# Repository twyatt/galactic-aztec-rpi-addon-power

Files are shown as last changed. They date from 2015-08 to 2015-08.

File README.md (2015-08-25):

# About

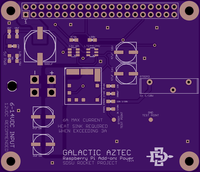
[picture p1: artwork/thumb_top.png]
OSHPark PCB Top Thumbnail

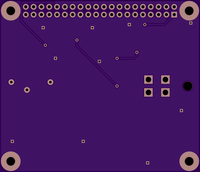
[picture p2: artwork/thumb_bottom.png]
OSHPark PCB Bottom Thumbnail


Board designed to provide external power (e.g. using 2-3S LiPo batteries) for Raspberry Pis onboard the [Galactic Aztec] rocket.

Supports 6-14 VDC input and allows tuning of output voltage between 4.64 and 5.27 VDC to the Raspberry Pi 5V GPIO pins.
**NOTE: RTRIM1 is incorrectly labelled as 2k and a 2.5k resistor should be used instead to put the output voltage at the expected range.**

The design features the [LTC4412HV] to act as an [ideal safety diode], which is advised for Raspberry Pi HATs.

*The hope was to utilize the power switch-over features of the [LTC4412HV], allowing for the Raspberry Pi to be powered via USB and upon disconnecting, automatically switch over to the auxiliary power input, but in testing this feature did not function properly. Power was drawn from both sources when connected rather than completely switching between the available power sources.*

Custom EagleCAD parts on this board can be found in the [SDSU Rocket Eagle Libraries].

# Bill of Materials

| Qty | Name | Description | Part Number | Vendor |
|:---:|---|---|---:|---|
| 1 | CI2 | Capacitor 47µF 35V 63mA SMD | [493-2202-1-ND] | DigiKey  |
| 1 | CI1 | Capacitor 22µF 35V 45mA SMD | [493-9805-1-ND] | DigiKey  |
| 1 | R1 | Resistor 100kΩ 1/4W 1% 0603 | [RHM100KADCT-ND]  | DigiKey  |
| 1 | IC1 | DC to DC Converter 6A | [555-1125-1-ND] | DigiKey  |
| 1 | RTRIM1 | Resistor 2kΩ 0603 | [P2.00KHCT-ND] | DigiKey  |
| 1 | RTRIM2 | Resistor 2.49kΩ 0603 | [RHM2.49KCFCT-ND] | DigiKey  |
| 1 | RTRIM3 | Potentiometer 1kΩ 10% 3/4W 20 | [987-1160-ND] | DigiKey  |
| 1 | RTRIM_ALT | Resistor 1.33kΩ 0.1% 1/10W 0603 | [P1.33KDBCT-ND] | DigiKey  |
| 1 | RTUNE | Resistor 220Ω 1% 1/10W 0603 | [RHM220CFCT-ND] | DigiKey  |
| 1 | CTUNE | Capacitor 3900pF 25V 5% | [445-2665-1-ND] | DigiKey  |
| 2 | CO1, CO2  | Capacitor 47µF 35V 63mA SMD | [493-2202-1-ND] | DigiKey  |
| 3 | C[2-4] | Capacitor 10µF 16V 0603 | [490-7198-1-ND] | DigiKey  |
| 1 | R3 | Resistor 470kΩ 1% 1/4W 0603 | [P470KBYCT-ND] | DigiKey  |
| 1 | IC2 | LTC4412HV Source Selector Switch IC SOT-23-6 | [LTC4412HVIS6] | DigiKey  |
| 1 | | MOSFET P-Channel 1.8V Vdss=12V Id=6A SOT23-6 | [FDC606PCT-ND] | DigiKey  |
| 1 | | Capacitor 1000µF 20% 10V 310mA SMD | [493-2171-1-ND] | DigiKey  |
| 1 | | Capacitor 820µF 20% 16V 80mΩ 510mA SMD | [1189-2069-1-ND]  | DigiKey  |
| 1 | | Capacitor 10uF 20% 16V 0603 | [490-7198-1-ND] | DigiKey  |
| 1 | | Molex Mini Fit Jr. 4-pos Right Angle | [WM1352-ND] | DigiKey  |
| 1 | D4 | LED Red Vf=1.8V If=2mA 0603 | [475-1195-2-ND] | DigiKey  |
| 1 | R4 | Resistor 1.8kΩ 1/4W 1% 0603 | [P1.8KBYCT-ND] | DigiKey  |
| 1 | | Header Stacking 2x20 Tall 23mm | [1979] | Adafruit |

[Galactic Aztec]: http://rocket.sdsu.edu/rockets
[LTC4412HV]: http://www.linear.com/product/LTC4412HV
[ideal safety diode]: https://github.com/raspberrypi/hats/blob/master/designguide.md#back-powering-the-pi-via-the-j8-gpio-header
[SDSU Rocket Eagle Libraries]: https://github.com/twyatt/SDSURocket-Eagle-Libraries
[493-2202-1-ND]: http://www.digikey.com/product-detail/en/UWT1V470MCL1GS/493-2202-1-ND/590177
[493-9805-1-ND]: http://www.digikey.com/product-detail/en/UWJ1V220MCL1GB/493-9805-1-ND/3963137
[RHM100KADCT-ND]: http://www.digikey.com/product-detail/en/ESR03EZPF1003/RHM100KADCT-ND/1983754
[555-1125-1-ND]: http://www.digikey.com/product-detail/en/APTS006A0X-SRZ/555-1125-1-ND/1766113
[P2.00KHCT-ND]: http://www.digikey.com/product-detail/en/ERJ-3EKF2001V/P2.00KHCT-ND/198219
[RHM2.49KCFCT-ND]: http://www.digikey.com/product-detail/en/MCR03ERTF2491/RHM2.49KCFCT-ND/2796475
[987-1160-ND]: http://www.digikey.com/product-detail/en/89PR1KLF/987-1160-ND/2408738
[P1.33KDBCT-ND]: http://www.digikey.com/product-detail/en/ERA-3AEB1331V/P1.33KDBCT-ND/3075785
[RHM220CFCT-ND]: http://www.digikey.com/product-detail/en/MCR03ERTF2200/RHM220CFCT-ND/2796470
[445-2665-1-ND]: http://www.digikey.com/product-detail/en/C1608C0G1E392J080AA/445-2665-1-ND/970490
[493-2202-1-ND]: http://www.digikey.com/product-detail/en/UWT1V470MCL1GS/493-2202-1-ND/590177
[490-7198-1-ND]: http://www.digikey.com/product-detail/en/GRM188C81C106MA73D/490-7198-1-ND/3900421
[P470KBYCT-ND]: http://www.digikey.com/product-detail/en/ERJ-PA3F4703V/P470KBYCT-ND/5036197
[LTC4412HVIS6]: http://www.digikey.com/product-detail/en/LTC4412HVIS6%23TRMPBF/LTC4412HVIS6%23TRMPBFCT-ND/3232334
[FDC606PCT-ND]: http://www.digikey.com/product-detail/en/FDC606P/FDC606PCT-ND/1626185
[493-2171-1-ND]: http://www.digikey.com/product-detail/en/UWT1A102MNL1GS/493-2171-1-ND/590146
[1189-2069-1-ND]: http://www.digikey.com/product-detail/en/16TKV820M10X10.5/1189-2069-1-ND/3986988
[490-7198-1-ND]: http://www.digikey.com/product-detail/en/GRM188C81C106MA73D/490-7198-1-ND/3900421
[WM1352-ND]: http://www.digikey.com/product-search/en?x=0&y=0&lang=en&site=us&keywords=538-39-30-1040
[475-1195-2-ND]: http://www.digikey.com/product-detail/en/LS%20L29K-H1J2-1-Z/475-1195-1-ND/810356
[P1.8KBYCT-ND]: http://www.digikey.com/product-detail/en/ERJ-PA3F1801V/P1.8KBYCT-ND/5036145
[1979]: http://www.adafruit.com/products/1979

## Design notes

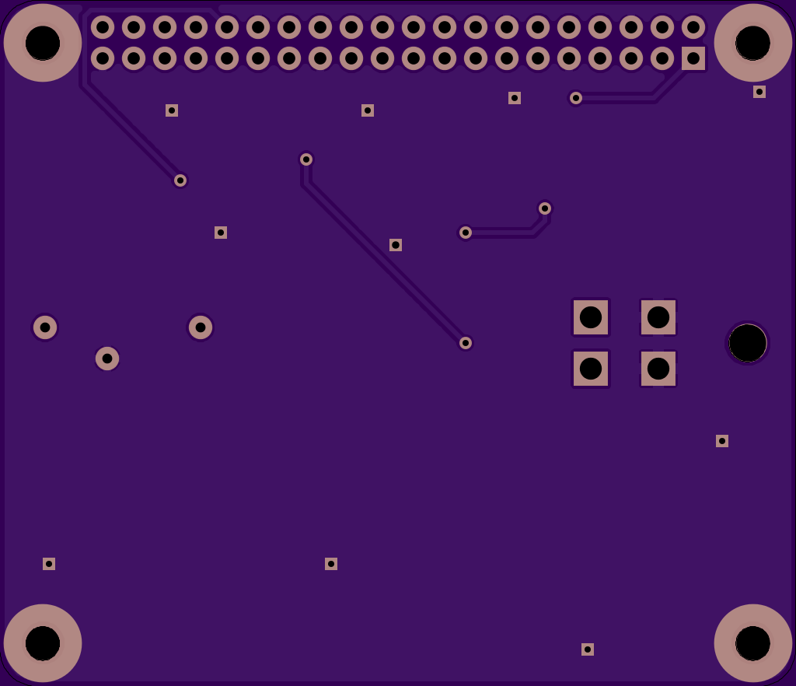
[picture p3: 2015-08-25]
artwork/bottom.png

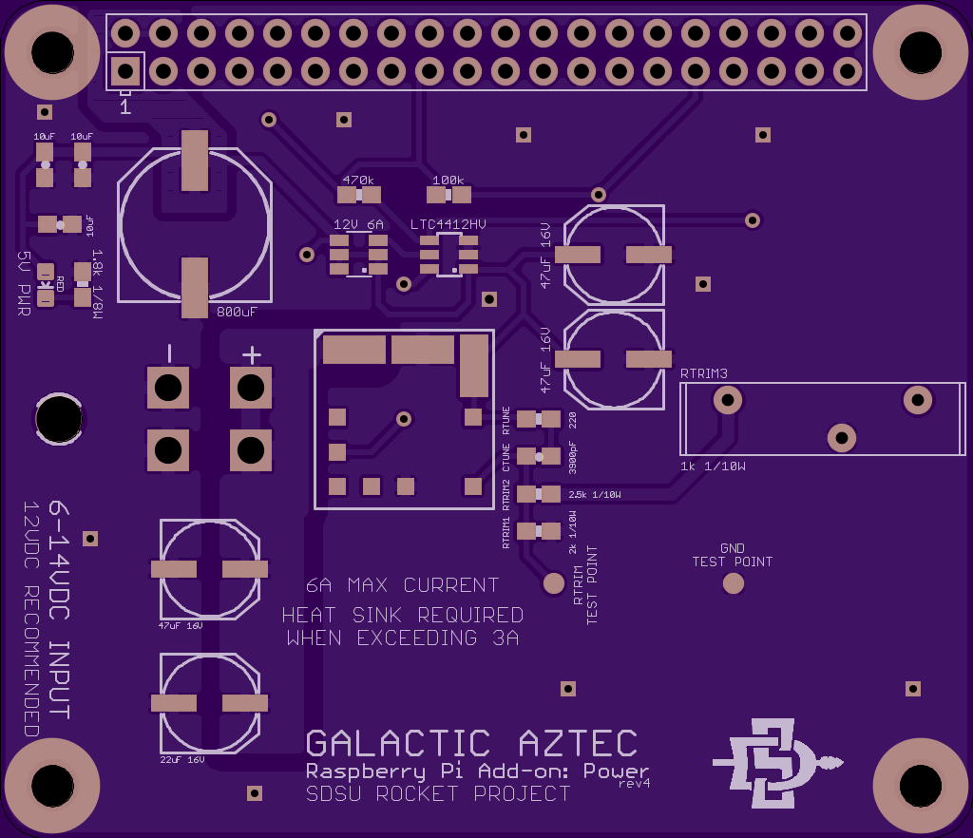
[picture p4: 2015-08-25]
artwork/top.png

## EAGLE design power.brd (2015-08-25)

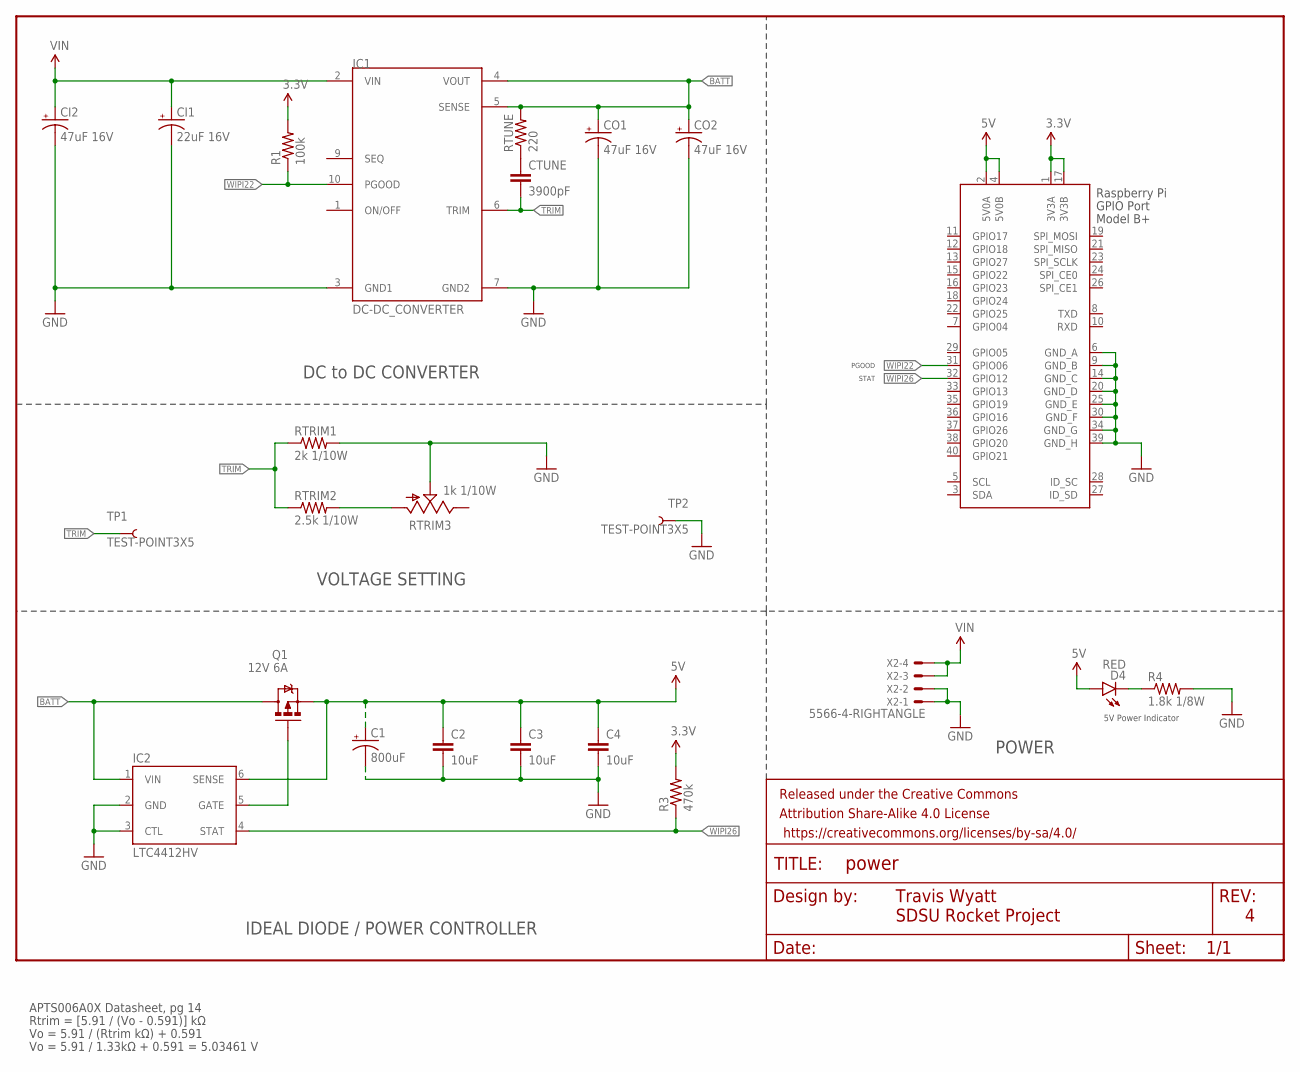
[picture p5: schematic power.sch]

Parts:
C1: 800uF; PANASONIC_G
C2, C3, C4: 10uF; 0603-CAP
CI1: 22uF 16V; NIPPON_F80
CI2: 47uF 16V; NIPPON_F80
CO1, CO2: 47uF 16V; NIPPON_F80
CTUNE: 3900pF; 0603-CAP
D4: RED; LED-0603
FRAME1: FRAME-LETTER; CREATIVE_COMMONS
IC1: DC-DC_CONVERTER
IC2: LTC4412HV; SOT23-6
Q1: 12V 6A; SSOT-6L
R1: 100k; 0603-RES
R3: 470k; 0603-RES
R4: 1.8k 1/8W; 0603-RES
RTRIM1: 2k 1/10W; 0603-RES
RTRIM2: 2.5k 1/10W; 0603-RES
RTRIM3: 1k 1/10W; 89P
RTUNE: 220; 0603-RES
TP1, TP2: TEST-POINT3X5; PAD.03X.05
X2: 5566-4-RIGHTANGLE; 5566-4
X3: RASPI_BOARD_B+#_H; RASPI_BOARD_B+HAT

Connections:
3.3V: R1.2, R3.2, X3.1 (3V3A), X3.17 (3V3B)
5V: C1.+, C2.1, C3.1, C4.1, D4.A, IC2.6 (SENSE), Q1.4 (S), X3.2 (5V0A), X3.4 (5V0B)
BATT: CO1.+, CO2.+, IC1.4 (VOUT), IC1.5 (SENSE), IC2.1 (VIN), Q1.1 (D), Q1.2 (D), Q1.5 (D), Q1.6 (D), RTUNE.2
GND: C1.-, C2.2, C3.2, C4.2, CI1.-, CI2.-, CO1.-, CO2.-, IC1.3 (GND1), IC1.7 (GND2), IC2.2 (GND), IC2.3 (CTL), R4.2, RTRIM1.2, RTRIM3.2 (S), TP2.P$1, X2.1, X2.2, X3.6 (GND_A), X3.9 (GND_B), X3.14 (GND_C), X3.20 (GND_D), X3.25 (GND_E), X3.30 (GND_F), X3.34 (GND_G), X3.39 (GND_H)
unnamed: IC2.5 (GATE), Q1.3 (G)
unnamed: CTUNE.1, RTUNE.1
unnamed: RTRIM2.2, RTRIM3.1 (A)
unnamed: D4.C, R4.1
TRIM: CTUNE.2, IC1.6 (TRIM), RTRIM1.1, RTRIM2.1, TP1.P$1
VIN: CI1.+, CI2.+, IC1.2 (VIN), X2.3, X2.4
WIPI22: IC1.10 (PGOOD), R1.1, X3.31 (GPIO06)
WIPI26: IC2.4 (STAT), R3.1, X3.32 (GPIO12)

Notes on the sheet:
Rtrim = [5.91 / (Vo - 0.591)] kΩ
Vo = 5.91 / (Rtrim kΩ) + 0.591
Vo = 5.91 / 1.33kΩ + 0.591 = 5.03461 V
APTS006A0X Datasheet, pg 14
5V Power Indicator
POWER
Travis Wyatt
SDSU Rocket Project
DC to DC CONVERTER
VOLTAGE SETTING
IDEAL DIODE / POWER CONTROLLER
STAT
PGOOD

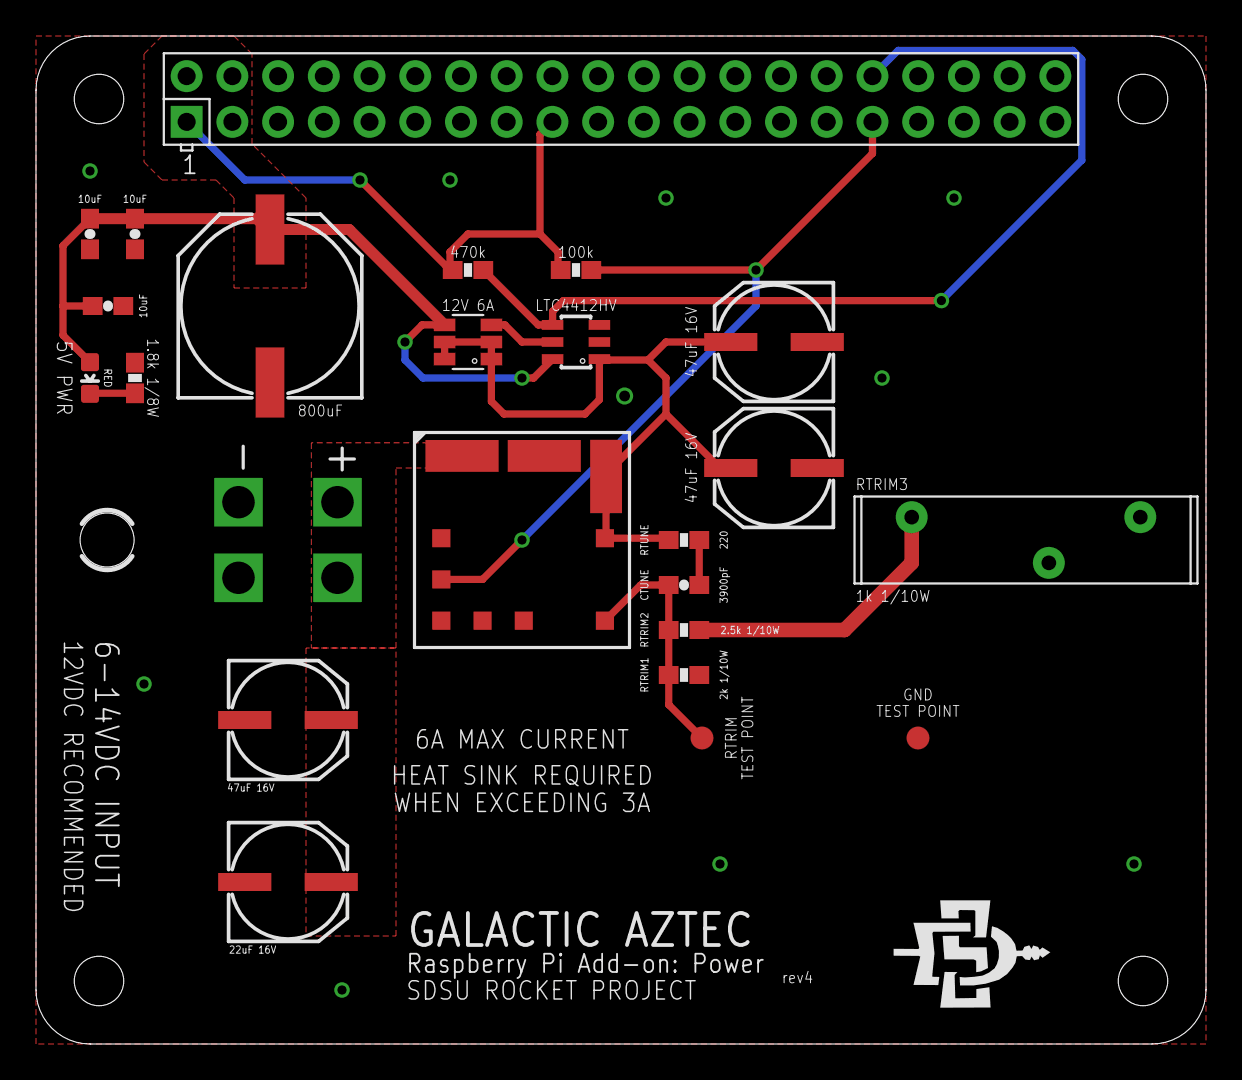
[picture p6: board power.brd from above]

Board: 2 copper layers, 65.0 x 56.0 mm, 25 parts (0 on the bottom side), 12 nets.

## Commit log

2015-08-22 Fix molex connector thru hole size
    [power.brd, power.sch]
2015-08-25 Add DC to DC converter and ideal safety diode
    [power.brd, power.sch]
2015-08-25 Optimize design and add voltage tuning
    Updated design for more capacitor reuse and added additional capacitors
    to help stabilize power. Added variable resistor to allow for fine
    tuning voltage output. Improved labeling of components on the schematic.
    [power.brd, power.sch]
2015-08-25 Fix variable resistor thru holes
    The thru hole positions and size for the variable resistor (RTRIM3) were
    fixed to have the component sit on the top side of the board.
    [power.brd, power.sch]

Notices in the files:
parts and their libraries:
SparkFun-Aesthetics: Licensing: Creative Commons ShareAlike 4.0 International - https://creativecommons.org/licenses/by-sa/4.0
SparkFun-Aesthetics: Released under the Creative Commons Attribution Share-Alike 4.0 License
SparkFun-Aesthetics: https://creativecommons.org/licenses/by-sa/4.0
